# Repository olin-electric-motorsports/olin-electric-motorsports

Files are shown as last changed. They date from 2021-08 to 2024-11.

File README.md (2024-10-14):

<h1 align="center">
	Olin Electric Motorsports
</h1>

Welcome to the Olin Electric Motorsports monorepo. This is the home for all of our
electrical, firmware, and software work.

This document will help you get started contributing and walk you through
important steps for collaborating with teammates.

## Getting Started

### For new members:
Make sure you have a GitHub account. If you don't, create one on [GitHub](github.com) (this website). Make sure to save your username, email, and password. This will be useful in the next step. Once you have an account, STOP, and ask a lead/senior engineer to add you to the `olin-electric-motorsports` org.

Once you've successfully installed Ubuntu, have a GitHub account, and have ben added as an org member: on your computer, open a terminal (press the Windows key and type `term`, then hit `Enter`).

Install `git` on your computer if it's not already.
```shell
sudo apt install git -y
```

Also install python3
```shell
sudo apt update && sudo apt install python3
```

One last Python library...
```shell
sudo apt-get install python3-distutils
```

### Linking a Computer to your Account
We need to connect your GitHub account to your computer's specific git instance \(created by the command you just ran\). We do this for safety: someone pretending to be you can't add code to our repo!
1. Set your username:
```shell
git config --global user.name 'your username here'
```

2. Set your email address:
```shell
git config --global user.email 'your email here'
```

3. Create the SSH Key \(essentially a super crazy passord\). When you’re prompted to "Enter a file in which to save the key," press `Enter`. This accepts the default file location. At the password prompt, hit `Enter` again.
```shell
ssh-keygen -t ed25519 -C "your_email@example.com"
```

4. To see your SSH Key, run the following command. Copy the whole contents of the output to your clipboard (you won't be able to copy or paste in the terminal using ctrl+c and ctrl+v, instead use ctrl+shift+c and ctrl+shift+v or right-click to do it graphically).
```shell
cat ~/.ssh/id_ed25519.pub
```

5. In your github page, go to your profile \(Top Right\) > `settings` > `SSH and GPG Keys`. Click on the green `New SSH Key` button. Title your key as `Olin Computer` and paste in your SSH key. Finally, click the green `Add SSH Key` button. Nearly done!
6. Test your ssh connection by using the command below. Type `yes` when prompted. You've done this step correctly if you see something along the lines of `Hi "username"! You've successfully authenticated, but GitHub does not provide shell access.`
```shell
ssh -T git@github.com
```
### Creating your OEM environment
Clone this repository into a folder of your choice (many people
choose to put it in `~/Documents`.

```shell
cd ~/Documents
git clone git@github.com:olin-electric-motorsports/olin-electric-motorsports.git
```

Once you have it, cd into the repo and install the KiCad Git filters (a set of rules that remove temp files that can cause clutter):

```shell
cd olin-electric-motorsports/
./scripts/install_kicad_git_filters.sh
```

You'll also want to have the KiCad Git Hooks to generate our symbol libraries. These hooks run every time you push or pull and allow multiple users to add symbols/footprints to our KiCAD library.

```shell
./scripts/install_kicad_git_hooks.sh
```

### Installing AVR and tools
Next, install the AVR toolchain:

```shell
sudo apt install gcc-avr avrdude avr-libc binutils-avr gdb-avr
```

### Installing Cantools
You need to be able to hear to our MCUs on the car!
```shell
pip3 install cantools
sudo apt install can-utils
```

### Installing Bazel

Next, install Bazelisk. Run this massive blob and you should be good to go.

```shell
sudo apt install apt-transport-https curl gnupg -y
curl -fsSL https://bazel.build/bazel-release.pub.gpg | gpg --dearmor >bazel-archive-keyring.gpg
sudo mv bazel-archive-keyring.gpg /usr/share/keyrings
echo "deb [arch=amd64 signed-by=/usr/share/keyrings/bazel-archive-keyring.gpg] https://storage.googleapis.com/bazel-apt stable jdk1.8" | sudo tee /etc/apt/sources.list.d/bazel.list
sudo apt install bazel-5.4.0
```

You should now be able to run the following without error (after changing your directory to be in
the `olin-electric-motorsports` folder):

```shell
bazel build --config=16m1 //examples/16M1/blinky -c opt
```

> [!NOTE]
> If you get an error message stating 'env: python: No such file or directory', ensure that the PATH environment variable is properly established. This can be done by adding the file to your .bashrc file:
> ```
> export PATH=$PATH:/usr/local/bin
> ```

### KiCad Setup

To install KiCad on Ubuntu, run the following: Type `Y` when prompted.

```shell
sudo add-apt-repository --yes ppa:kicad/kicad-8.0-releases
sudo apt update
sudo apt install --install-recommends kicad
```

Open KiCad (windows key and type KiCAD) Click on the Blue App (always do this when opening Kicad - otherwise you can corrupt files!). Hit `Enter` if asked about settings imports and auto-updates for add-ons.
From the top bar, open _Preferences > Configure Paths..._. Add a new row to the table using the plus button (you will have to fill out TWO fields... shown below):

Name | Path
-----|-----
OEM\_DIR|`/home/your-username/Documents/olin-electric-motorsports`

Click `OK`, then again from the top bar, open _Preferences > Manage Symbol Libraries ..._.
Same deal as before with the new line at the bottom, new values though this time:

Name | Path
-----|-----
OEM |`${OEM_DIR}/parts/schematic/oem.kicad_sym`

> [!WARNING]
> If you get an error, you either typed something incorrectly or haven't generated the OEM symbol library ever before.
> To generate:
> 1. navigate to the base `olin-electric-motorsports` directory in a terminal.
> 2. run python3 tools/symbols/convert.py symbols2library
> 3. path to symbol files: parts/schematic/oem
> 4. path to library file: parts/schematic/oem.kicad_sym

Click `OK`, then again from the top bar, open _Preferences > Manage Footprint Libraries ..._.
3rd time's the magic one, plus button, add the values in the table below.

Name | Path
-----|-----
OEM |`${OEM_DIR}/parts/oem.pretty`

where `your-username` is the username on your computer.
If you cloned our repository into a different directory than the `~/Documents` folder, this is just an absolute path to the repo.

Visit [this page](https://www.kicad.org/download/) to find instructions for
downloading KiCad for other operating systems.

## Integration Resources
### Flashing to microcontrollers

> [!CAUTION]
> Take care to plug in the programmer correctly. If you insert it the wrong way, you have the potential to reverse-bias sensitive electronics (you could smoke them)!

To flash (program) an ATMEGA16m1 microcontroller, use a variation of the following command:
```shell
need to insert example flashing command here
```

To flash (program) an ATMEGA16m1 microcontroller using the btldr (remote CAN flashing), use a variation of the following command:
```shell
need to insert example can flashing command here
```

### Viewing CAN data/the canviewer
First, plug a CAN-to-USB dongle into your computer and connect CAN+ and CAN- to the car or test platform's CAN port.

To initalize the dongle, run the following command:
```shell
need to insert example can init command here
```

### Cantools
1. `candump`: A tool for streaming CAN frames as they are sent. Useful for short captures or slow data.
2. `cansniffer`: Similar to candump, but messages with the same ID replace each other for easier viewing (a table).
3. `cansend`: Use this tool to send CAN frames from your computer. CAN (oh the puns will never end) be helpful when debugging boards or to program modules like the motor controller or G-Meter.

### CANViewer
OEM has designed a custom Python CAN GUI to monitor the car's state.
Type the following command to run the viewer.
```shell
need to insert CANViewer command here.
```

### Contributing

If you are working on a new project, the first step is to make sure you have the
latest code:

```shell
git pull origin main
```

### Onboarding stop here...

Next, create your feature branch (only do this once you have a project!):

```shell
git switch -c your-username/feature-name origin/main
```

Now, you can start working on code, committing on your branch, and eventually
opening up a pull request to `main`.

New projects should be placed into a folder within the `//projects` directory
(for instance, `//projects/hitl/`. Hardware and firmware that run on MKV or MKVI
should go in the proper subfolder within `//vehicle`.

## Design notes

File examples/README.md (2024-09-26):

# Examples

The `examples/` directory will house code samples and hardware samples for
people to reference. Examples will include

* Blinky for the ATMega16m1
* Blinky for the STM32F103C8T6 (not finished)
* Simple ATMEGA KiCad schematic/layout (not finished)

as well as others.

## To-Do

* Who will own this folder? Who will keep it up to date, add new content, make
  sure things are correct, etc?

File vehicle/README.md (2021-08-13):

# Vehicle

The boards and code for the different vehicles that the team builds will exist
in this folder.

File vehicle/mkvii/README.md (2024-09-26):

# MKVI

The development of boards for the Mark VII car will go in this folder.
Here's to a great year everyone!

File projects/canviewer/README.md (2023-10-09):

# OEM CAN Dashboard

Welcome! Here lies the documentation for the use of the CAN dashboard GUI on our team.

The dashboard uses a QT GUI and includes support for SocketCan (for example, the PCAN dongles) as well as our new Seeedstudio dongles.

It also is fully configurable via YAML.

## Using the tool
1. Set up your CAN device if you are using a PCAN or other socketcan device. Instruction for this can be found [here](https://coda.io/d/_dbuFnC2EA_e/How-to-use-CAN_suzvC)
    - You can also use this tool with a virtual CAN bus
2. Run the tool! This is done using the command `bazel run //projects/canviewer`. There are three command line arguments as well
    - `-b` - Either `seeedstudio` or `socketcan` 
    - `-c` - Channel
        - Socketcan: this is the network interface name you created when setting up your device (usually can0 for real hardware or vcan0 for a virtual CAN bus)
        - Seeedstudio: this is the _device path_ for your CAN dongle. Typically this will be something like `/dev/ttyUSB0`. The best way to find it is to run `ls /dev/ttyUSB*`, which lists all the USB device paths, before and after you plug in your dongle to find the one that was added. The number starts at 0 and increments every time something is plugged in, so if you unplug and replug your CAN dongle, the number will change!
    - `-d` - the DBC file to be used to decode the CAN messages. This is specified as a file path starting from the root of the monorepo.
        - This has a default value of `vehicle/mkvi/mkvi.dbc` - in other words, if you want to decode messages from MKVI or a MKVI board, you do not need to specify this argument. If you're reading this in future years, feel free to update the default value in a new PR - just be sure to add your DBC as a dependency in the BUILD file for this project.
        - You can check `//vehicle/mkvi/BUILD` to see which DBC/YAML files are included in the master DBC
    - These arguments would be passed like so for a bustype of seeedstudio and a USB device at /dev/tty/USB0 when plugged into MKVI:
        ```
        bazel run //projects/canviewer -- -b seeedstudio -c /dev/tty/USB0
        ```
        The two dashes signal the end of the arguments to bazel and any remaining ones will be passed to the CAN viewer.
    
## Configuring the tool

To change the signals that are displayed in the first two columns, simply add or remove the signal names from underneath their respective column headers in the YAML. For example, if I wanted to see the IMD status in the Vehicle Values section, I would add this line under the vehicle values header
```
imd_status:
```
Note the colon at the end - it is required.

The states section is formatted like so:
```
air_control_critical: # Message name
  air_state: # State signal
  air_fault: # Fault Signal
```
Again, note the indentation and the colon - they are part of the YAML format.

If you would like to apply a processing function to process the value one of the signals in the vehicle values column before displaying it:
1. Define the function in the `projects/canviewer/utils.py` file
2. Specify it in the YAML by setting the signal's value to a dictionary with `processing_function` as a key and the function name as its value, like so:
```
# Vehicle Values
max_temperature:
  processing_function: convertVtoT
min_temperature:
  processing_function: convertVtoT
pack_voltage:
air_p_status:
...
```

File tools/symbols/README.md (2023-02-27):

# Symbol Converter

## Usage

### `symbols2library`
Convert symbols to `.kicad_sym` library.

If you have installed the git hooks (`./scripts/install_kicad_git_hooks`), this will run automatically after each `git checkout`.

Example:

```bash
bazel run //tools/symbols:convert -- symbols2library --source /mnt/data/Formula/olin-electric-motorsports/parts/schematic/oem -o /mnt/data/Formula/olin-electric-motorsports/parts/schematic/oem.kicad_sym
```

### `library2symbols`
Convert a `.kicad_sym` library to symbols.

If you have installed the git hooks (`./scripts/install_kicad_git_hooks`), this will run automatically during each `git commit` and add symbol files to the commit.

If you do not wish to have this happen you can `git commit --no-verify` instead and then manually run the script.

Example:

```bash
bazel run //tools/symbols:convert -- library2symbols --source /mnt/data/Formula/olin-electric-motorsports/parts/schematic/oem.kicad_sym -o /mnt/data/Formula/olin-electric-motorsports/parts/schematic/oem
```

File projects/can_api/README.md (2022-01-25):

# Generated CAN API

The purpose of this project is to create a tool that automatically generates C
code that abstracts CANbus interaction for microcontrollers.

## Context

Before 2021, our team used a CAN API that allowed for sending byte-arrays with a
specified ID. In 2021, we developed a new library that used semantics of the C
language like structs and enums to develop a cleaner library that allowed for
initializing, sending, and receiving messages, with options for polling and
interrupts.

However, none of these specified the IDs or the contents of the messages. For
that, we used the MKx CAN Address Space, a Google Sheet that listed all of the
messages and all the different signals. This was the "single source of truth"
that all the application code referenced.

The new generated CAN API is a layer of abstraction that utilizes the CAN
library as a network layer. Messages and their signals are defined in YAML
files.

## Scope

The project is designed to be _robust_ and as _reusable_ as possible. Most of
the project is unit-tested. The backend of the project uses an external library
called [cantools](https://github.com/cantools/cantools), which is thoroughly
tested.

### Goals

* A DBC file can be generated from the individual YAML files
* All message collisions are detected at compile-time
* A `.c` and `.h` file are generated for each YAML file that include send and
  receive functions for each of the messages sent and received by the ECU as
  specified by the YAML file

### Non-goals

* _Getters_ and _setters_: Functions of these types are used to set the values
  of signals in a CAN message (like `set_bspd_brakelight_voltage(uint16_t
  voltage)`). These could be useful, but for now, we opt to use global variables
  because they have a simpler implementation.
* Message ID assignment: This could be a future goal, see __Future Work__ below

## Usage

To begin, we must define a YAML file for the ECU. As an example, we will use the
BMS ECU. The file we are writing will be in `vehicle/mkv/software/bms/bms.yml`.
We begin with the name of the node/ECU, _bms_:

```yaml
# vehicle/mkv/software/bms/bms.yml
name: bms  # Name of the ECU
```

Next we specify the messages received by the ECU. For example, the BMS should
receive the AIR Control Critical message, so we can specify the following:

```yaml
# All the received messages
subscribe:
  - name: air_control_critical
    mob: 1
```

This says that the BMS should listen for the `air_control_critical` message
(this name is specified as the `name` of a message in a different YAML file),
and that it should use message object (MOb) 1.

__Note that this code _only_ allows for receiving a specific CAN message per
MOb, not multiple. If you need to listen to a range of messages, don't use the
API.__

Now we specify the messages _sent_ by the ECU. Let's take the following row from
the MKV CAN Address Space as an example:

Name | ID | Length | Frequency (Hz) | Byte0 | Byte1 | Byte2 | Byte3 | Byte4 | Byte5 | Byte6 | Byte7
-----|----|--------|----------------|-------|-------|-------|-------|-------|-------|-------|------
BMS Core|0x10|8|16|Fault Code|Relay Status|Temperature|Pack Voltage|SOC Estimate|BMS OK|Current-limiting enabled|Cell-balancing status

The MKV CAN Address space specified that the minimum size of any signal is 1
byte. However, with our system, we can have signals that are smaller (like a
single bit). Here's how we might represent the message in a new way:

```yaml
publish: - name: bms_core
    id: 0x10
    freq_hz: 16
    signals:
      - name: fault_code
        slice: 0 + 8  # This is (start bit) + (length)
        unit:
          type: enum
          values:
            - NO_FAULT
            - FAULT_EXAMPLE_1
            - FAULT_EXAMPLE_2
            - ...
      - name: temperature
        slice: 8 + 8
        unit:
          type: uint8_t  # C-type that this is stored as
          name: degC  # Used for displaying when decoding information
          offset: 0  # Offset used to calculate the true value
          scale: 5 / 4096  # Scale used to calculate the true value
      - name: pack_voltage
        slice: 16 + 8
        unit:
          type: uint8_t
          name: V
          offset: 0
          scale: 1000
      - name: soc  # State of Charge
        slice: 24 + 8
        unit:
          type: uint8_t
          name: "%"
          offset: 0
          scale: 100 / 4096
      - name: relay_state
        slice: 32 + 1
        unit:
          type: bool  # Bool is used for any value where it is either 0 or 1
          values:
            t: Relay open  # String to display when value is true
            f: Relay closed  # When value is false
      - name: bms_ok
        slice: 33 + 1
        unit:
          type: bool  # Bool is used for any value where it is either 0 or 1
          values:
            t: BMS OK
            f: BMS NOT OK
      - name: current_limiting_enabled
        slice: 34 + 1
        unit:
          type: bool  # Bool is used for any value where it is either 0 or 1
          values:
            t: Current limiting enabled
            f: Current limiting disabled
      - name: cell_balancing_status
        slice: 35 + 1
        unit:
          type: bool  # Bool is used for any value where it is either 0 or 1
          values:
            t: Cell balancing active
            f: Cell balancing inactive
```

Notice that we have reordered some of the fields. This is because it is better
to group signals together if they are less than a byte so that they can be
"packed" together. If we had a 1-bit signal followed by an 8-bit signal followed
by a 1-bit, it would require at least 3 bytes of space since full bytes must be
aligned.

Now that we have our completed file, we can define our CAN API using Bazel. In
the `BUILD` file, we will load a rule and create a new target:

```python
# vehicle/mkv/software/bms/BUILD

load("//bazel/tools:defs.bzl", "can_api_files")

...

# Must include this
exports_files([
    "bspd.yml",
])

# Defines the CAN API library
can_api_files(
    name = "can_api",
    dbc = "//vehicle/mkv:mkv.dbc",
    yaml = ":bspd.yml",
)
```

In addition, we should add the BMS YAML file to the list of MKV YAML files in
`vehicle/mkv/BUILD`:

```python
# vehicle/mkv/BUILD
load("//bazel/tools:defs.bzl", "dbc_gen")

# Generates DBC
dbc_gen(
    name = "mkv.dbc",
    srcs = [
        "//vehicle/mkv/software/air_control:air.yml",
        "//vehicle/mkv/software/brakelight_bspd:bspd.yml",
        "//vehicle/mkv/software/motor_controller:motor_controller.dbc",

        # New
        "//vehicle/mkv/software/bms:bms.yml",
    ],
)
```

We do this so that we can use the DBC generator to link all of these YAML files
together into a single DBC.

Now that we have our CAN API created, we can test to make sure that it works:

```shell
$ bazel build //vehicle/mkv/software/bms:can_api
```

If this builds successfully, then the CAN API generation is working.

We can add `:can_api` to the `deps` field of our `cc_firmware` that defines the
BMS code. Then, in our BMS file, we can start using the API. The following
features are documented:

#### Setting signal values

In order to set the value of a signal, we use a struct. The CAN API generates a
struct whose fields are each of the signals of the message. For example, the
struct for the `bms_core` message defined above might look like:

```c
struct can_tools_bms_core_t {
    uint8_t fault_code;
    uint8_t temperature;
    uint8_t pack_voltage
    uint8_t soc;
    uint8_t relay_state;
    uint8_t bms_ok;
    uint8_t current_limiting_enabled;
    uint8_t cell_balancing_status;
};
```

__Note that even though the length of, for example, `relay_state` should be 1
according to the YAML, the struct will store it as a byte. This is because
before the message is sent using the `can_send` function, there is another,
private function that "packs" the message according to the correct lengths. So
the value of the `uint8_t relay_state` will be packed into a single bit when the
message is sent__.

The CAN API also defines a single variable of this type as `struct
can_tools_bms_core_t bms_core`. That way, you can access it like so:

```c
// Set the pack_voltage
bms_core.pack_voltage = get_pack_voltage();

// Set the relay_state
bms_core.relay_state = gpio_get_pin(BMS_RELAY);
```

This is the same variable that is used when sending the CAN message, so care
should be taken that there are no concurrency issues (say, if a value is set
during an interrupt which occurs while a CAN message is being sent).

#### `can_init_{ecu}`

This replaces/wraps the `can_init` function. Currently, there is no additional
functionality, but in the future it could be used to initialize certain
ECU-specific things, or could be useful if more than one CAN bus existed on the
car.

#### `can_send_{message}`

This sends a specific CAN message. For example, to send the _BMS Core_ CAN
message, we could call `can_send_bms_core();`. This will take the aforementioned
`bms_core` variable (with all of the signals as struct fields), pack it into a
byte array, and send it as a CAN message.

#### `can_receive_{message}`

This receives a specific CAN message. In order to receive the _BMS Core_
message, we call `can_receive_bms_core();`. This function will return
immediately. The following table gives the return codes:

Return Code | Meaning
------------|--------
`0`|Data is ready
`1`|Fatal error occured
`-1`|Message not received

If a `0` is returned, we can access the data in the message struct (i.e.
`bms_core`).

### DBC Generation

The final feature of the project is DBC generation. As we saw, when we declare a
YAML file, we can also add it to the `srcs` of a `dbc_gen` target, like the one
in `vehicle/mkv/BUILD`. In general, we want to have one DBC per vehicle. In
order to build the MKV DBC, we can run:

```shell
$ bazel build //vehicle/mkv:mkv.dbc
```

Then we can access the DBC file in `bazel-bin/vehicle/mkv/mkv.dbc` and use it in
Wireshark, BusMaster, or any other software that uses a DBC.

## Concurrency

__⚠️ Important Usage Note. ⚠️__

The `can_send_{{ message }}` function must _not_ be called from an interrupt
context. If it is, there can be unpredictable behavior. In general, special care
should be taken around interrupts and concurrency. There is a global, `volatile`
variable for the CAN data containing each of the signals, and this struct is
used in the `can_send` function. Thus, if the `can_send` function happens in an
interrupt that occured when a variable was in the middle of being updated, the
data can become garbled.

The `can_send` function is wrapped in atomic block, meaning that during its
execution, no interrupts will occur.

## Future Work

In the future, it would be great if the IDs were automatically generated based
on message priority and deadline. There is a
[paper](https://www-users.cs.york.ac.uk/~robdavis/papers/RTNS2016_can_extend.pdf)
that describes an algorithm that can be used to optimally generate CAN IDs, and
this could be interesting to implement later on. But since our CANbus is so
under-utilized, there isn't really any urgency.

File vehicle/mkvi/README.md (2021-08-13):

# MKVI

The development of boards for the Mark VI car will go in this folder.

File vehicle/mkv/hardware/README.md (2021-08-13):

# Vehicle Hardware

The subfolders in this folder will be for the different PCBs that will go on the
car for the current season. This may be things like the BMS, the dashboard, and
the AIR control boards.

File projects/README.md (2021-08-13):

# Projects

The `projects/` directory will house projects that are under active and volatile
development. This will include things like advanced research projects that won't
make it onto the vehicle during the current season, _as well as_ projects that
are parallel to the car, like the HIL system.

Once a car-related project has matured enough, it will be moved into the
`vehicle/` directory, where development may continue to integrate it into the
vehicle of the season.

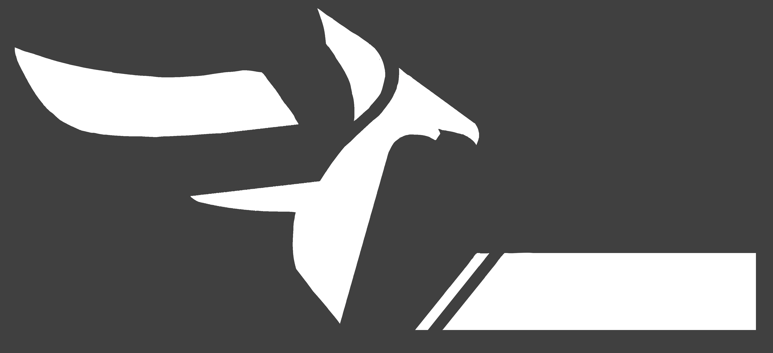
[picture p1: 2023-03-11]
vehicle/mkvi/hardware/service-section/motherboard/Art/WHITE_motherboard_a_top_pcb.png

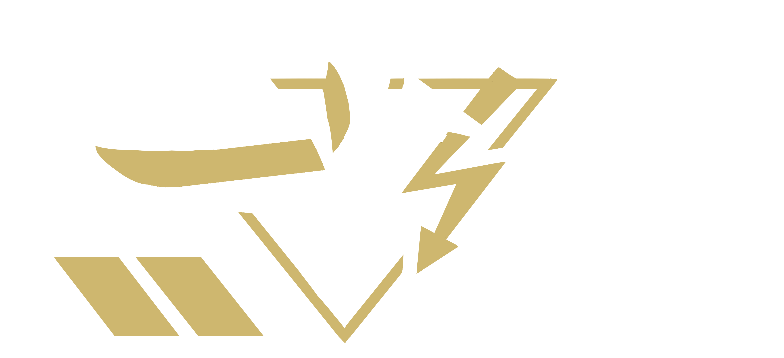
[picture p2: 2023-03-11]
vehicle/mkvi/hardware/service-section/motherboard/Art/GOLD_motherboard_a_top_pcb.png

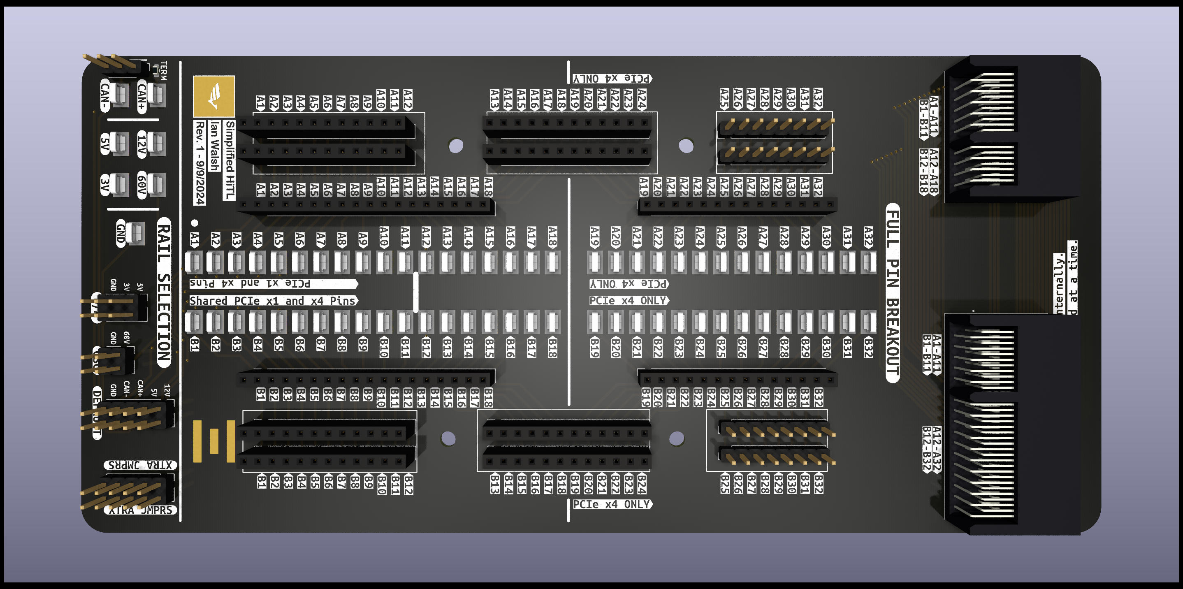
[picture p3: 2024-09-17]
projects/PCIe Development/pcie_breakout/breakout_pcie.png

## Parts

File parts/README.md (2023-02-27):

# KiCad Parts
KiCad library employed by Olin Electric Motorsports electrical team.

## Libraries

We are starting a fresh KiCad libraries for Mk. 6. The goal is to ensure that we do not incorporate components that are not stocked and to increase the quality and consistency of our libraries. The new library allows us to better track the status of components and support multiple purchasing options.

| Path | Description |
| ---- | --- |
| `/parts/3DModels/` | 3D Models for Mk. 5 era |
| `/parts/footprints.pretty/` | Footprints library for Mk. 5 era |
| `/parts/schematic/formula.kicad_sym` | Schematic symbol library for Mk. 5 era |
| `/parts/mk6.3dshapes/` | 3D Models for Mk. 6 |
| `/parts/mk6.pretty/` | Footprints library for Mk. 6 |
| `/parts/schematic/mk6.kicad_sym` | Schematic symbol library for Mk. 6|

## Guidelines

> Note: Some older parts do not follow this guidelines completely. For this reason, double check when copying over any legacy components.

1. General symbol naming guidelines

> Prior to Mk. VI we used a global library, however it was poorly maintained and many of the components are no longer available for purchase. New projects must use the OEM libraries.

Open KiCad. From the top bar, open up _Preferences > Manage Symbol Libraries..._. Add new rows to the table:

Nickname | Library Path
---|---
formula |`${OEM_DIR}/parts/schematic/formula.kicad_sym`
OEM | `${OEM_DIR}/parts/schematic/oem.kicad_sym`

From the top bar, open up _Preferences > Manage Footprint Libraries..._. Add new rows to the table:

Nickname | Library Path
---|---
footprints |`${OEM_DIR}/parts/footprints.pretty`
OEM | `${OEM_DIR}/parts/oem.pretty`

# Guidelines

## Symbols

Applies to all symbols in the `OEM` library. When a new schematic symbol is added it must be checked against these guidlines.

### Naming

For specific parts such as ICs, use the general part number (e.g. `ADBMS1818` not `ADBMS1818-WASZ-RL`). For passives and other generic components, a descriptive (e.g. `R_200`) name is suitable.

### Required Fields

Field | Example | Show |  Description
--- | --- | --- | ---
Reference | `R` | Y | [Letter corresponding to component type](https://klc.kicad.org/symbol/s6/s6.1/)
Value | `10K` | Y |  Value of component or part name
Footprint | `OEM:R_0805` | N | Reference to footprint for component
Datasheet | `https://www.example.com/.../datasheet.pdf` | N | Link to datasheet
MPN | `RCA080510K0FKEA` | N | Manufacturer Part Number for ordering
MFN | `Vishay` | N | Manufacturer (not to be confused with distributors like digikey)
DKPN | `541-2226-2-ND` | N | Digi-Key Part Number for ordering (name of disitributor if not available through DK)
Package | `0805` | N | Component package (if a common package)
NewDesigns | `Yes` | N | If the component should be used in new designs. If a component should not be used set to `DO NOT USE` and enable `Show`.
Stocked | `Tape` | N | Should we keep this part on hand, if so what format
Style | `SMD` | N | `SMD` or `THT` or `Custom`. Useful for filtering BOMs for assembly service

### Required Metadata

Property | Notes
--- | ---
Symbol Name | Do not include formula, OEM, MkVI, etc.
Description | Part description for search
Keywords | Comma separated list of search terms

### Component Specific Fields

In addition to the required fields, some component types have additional required fields to help with design reviews. If there is any specification you think is important to the component, add it as a field in addition to the required fields.

#### ICs

Field | Example | Show |  Description
--- | --- | --- | --- | 
SupplyVoltage | `2.5-5.5V` | N | The supply voltage for the IC
LogicLevel | `5V` | N | If applicable, the logic level for IO

#### Connectors

Field | Example | Show |  Description
--- | --- | --- | --- | 
RatedVoltage | `600VDC` | N | Rated voltage - must be documented in datasheet or link source
ContactCurrent | `.8A` | N | Rated current per contact
MatesWith | `MPNABCD` | N | Symbol name of mating connector. If there are multiple mating connectors `MatesWithAltX` fields may be added.

#### Passives

The relevant specifications vary for different passives. Make sure any specifications that were relevnt to your selection are included as fields and listed in the description. This makes finding suitable alternatives easier if there are supply issues.

### Symbol Design

1. If multiple pins should **always** be connected together, use [pin stacking](https://klc.kicad.org/symbol/s4/s4.3/).
    - Do not stack power pins if they require seprate decoupling capacitors
1. Pin orientation
    * Power pins must be placed on the top of the symbol
    * GND pins must be placed on the bottom of the symbol
    * Input pins must be placed on the left of the symbol
    * Output pins must be placed on thr right of the symbol
    * For some components, pins can function as inputs or outputs. In this case they should be placed on the right of the component.
1. Pins should be grouped functionally, not based on pin order

## Footprints

Applies to all footprints in the `OEM` library. When a new footprint is added it must be checked against these guidlines.

Do not create footprints for specific components, create footprints for packages so that they can be reused. Add alternate package names to the description.

In the rare case that a component does not have a package name, the symbol name must be matched exactly.

When possible, use KiCad's built-in footprints and save a copy to the OEM library. This ensures our library is stable and updates to built in packages do not unexpectedly break anything.

### Naming

We loosely follow the [KiCad Library Conventions for footprint names](https://klc.kicad.org/footprint/f3/). Generally, we err on the side of slightly simpler, easier to remember footprint names.

For example, we omit the metric sizing in SMT passives (i.e. `R_0805` instead of `R_0805_2012Metric`).

For connectors, we follow `[Series]_[PinLayout]_[Orientation]`. For example, `MicroFit_2x4_RA`.

Orientation | Shorthand
--- | ---
Vertical | VT
Horizontal | RA
45 degree | 45

### Required Fields

Field | Example | Show |  Description
--- | --- | --- | --- | 
Source `https://example.com/.../mpn.pdf` | N | Datasheet with footprint drawing.

### Required Metadata

Property | Notes
--- | ---
Symbol Name | Do not include formula, OEM, MkVI, etc.
Description | Part description for search. Include alternate package names
Keywords | Comma separated list of search terms

### Footprint Design
Getting footprints online is encouraged, but sometimes they aren't perfect.

1. On ICs, Pin 1 must be marked with two dots and an extended line over the pin. The dots must have a radius of 0.3mm.

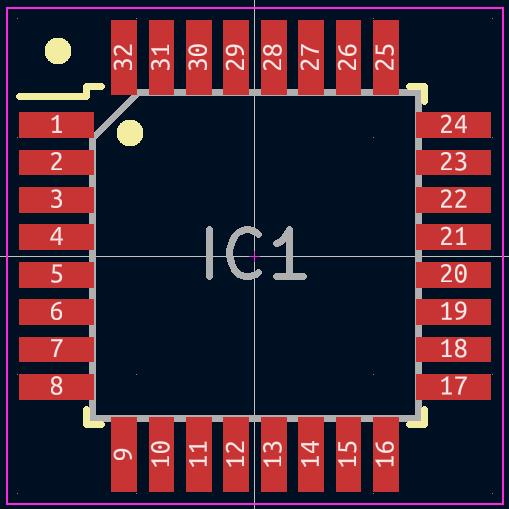
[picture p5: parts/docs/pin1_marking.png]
    
1. For polar components, the component outline must not extend around the anode. Additional markings should not be used.

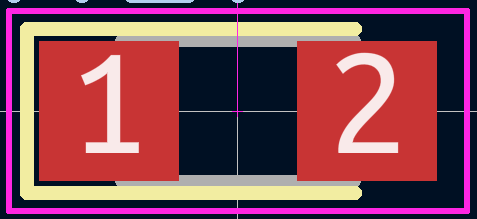
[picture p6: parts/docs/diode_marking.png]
screenshot of diode with marking
    
1. Through hole components must indicate pin 1 with a square pad.

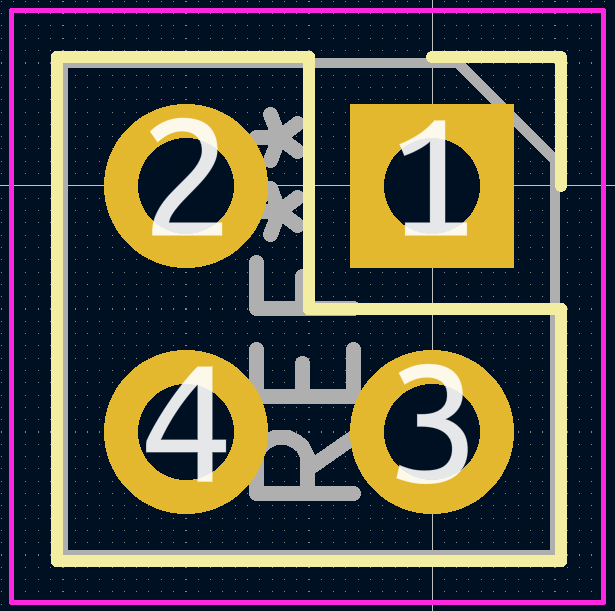
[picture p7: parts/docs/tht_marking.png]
    
1. Silksreen designs in component footprints must be drawn with a line width of 0.12mm.

1. The reference designator should be set to the `User.Comments` layer or hidden to avoid cluttering the silkscreen.

## 3DModels

All footprints must include a 3D Model.

All 3D Models must be placed in the `OEM.3dshapes`. Do not create subdirectories for individual 3D models. Add only the 3D model files required for each component. The name of each file must match the associated footprint. If multiple footprints use the same 3D model, the name should match the most generic footprint.

If possible, models should not require positioning or scaling to match the footprint.

* 3D Model Naming Guidlines

    The name of 3D Models should match the footprint name.

Guidelines are based off [KiCad Library Convention](https://klc.kicad.org/).

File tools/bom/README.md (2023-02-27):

# Unified BOM tool

## Usage

### `join`
Joins a number of BOMs into a single BOM grouped by DigiKey Part Number for ordering.

Requires a input CSV with columns `Name`, `Count`, `BOM`. Column names are case insensitive, order doesn't matter and additional columns will be ignored. The bom for each board is multipled by the desired count before joining into the final BOM. Each BOM must include `Count` and `DKPN` columns. This is useful for large batch order with multiple boards that share components. The resulting file can be edited to meet minimum quantities or add additional parts.

Example:

```bash
bazel run //tools/bom:join -- --map /mnt/data/Formula/olin-electric-motorsports/vehicle/mkvi/boards.csv -o /mnt/data/Formula/olin-electric-motorsports/vehicle/mkvi/bom.csv
```

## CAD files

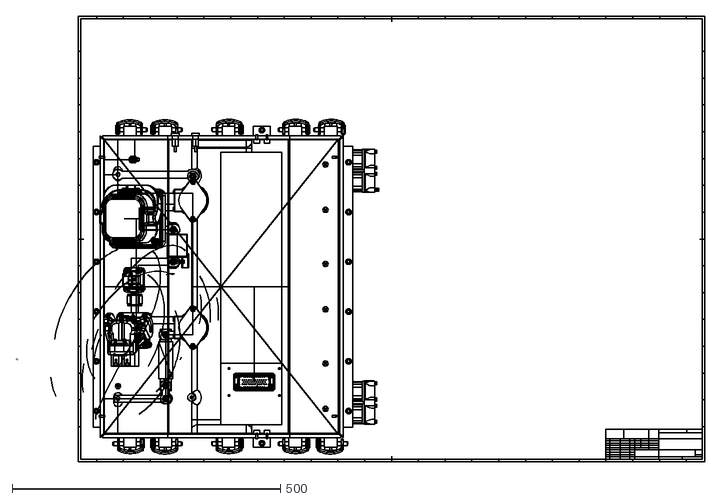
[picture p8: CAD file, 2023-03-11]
vehicle/mkvi/hardware/service-section/motherboard/6-AC0-ASSEMBLY-MOTHERBOARD-REFERENCE.DXF
1284.8 x 831.0

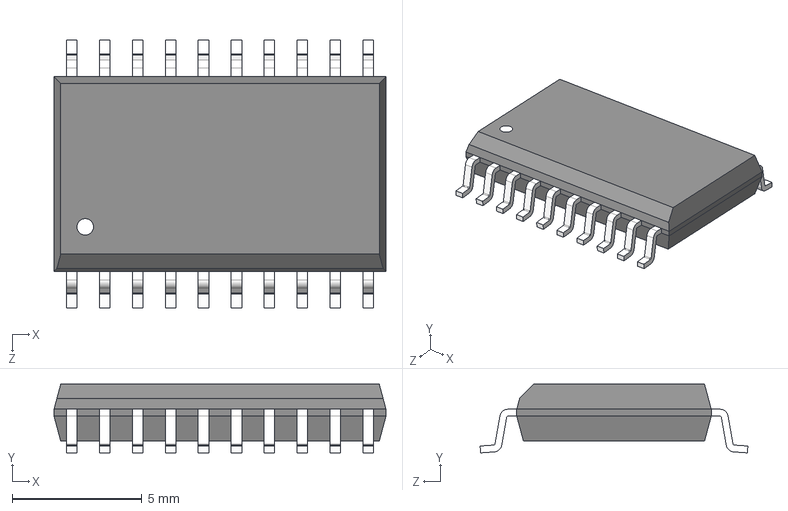
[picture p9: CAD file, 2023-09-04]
parts/3DModels/20-SOIC/20-SOIC.STEP
12.8 x 2.65 x 10.3 mm

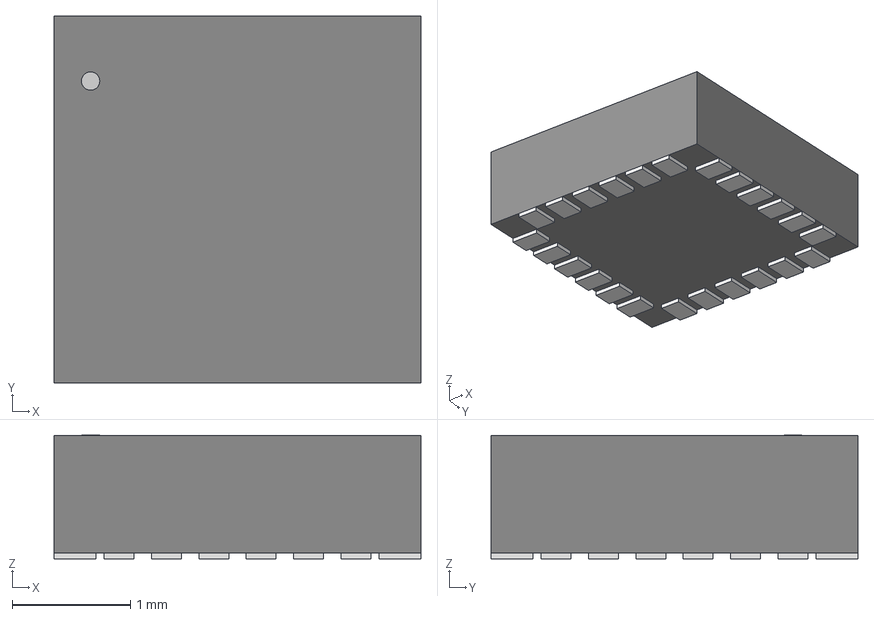
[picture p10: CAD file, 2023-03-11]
parts/3DModels/24-QFN/24-QFN.step
3.10 x 3.10 x 1.04 mm

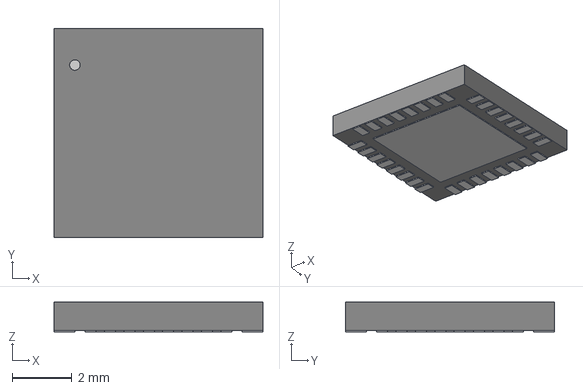
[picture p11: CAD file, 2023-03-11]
parts/3DModels/32-QFN/PV_ATM.step
7.00 x 7.00 x 1.00 mm

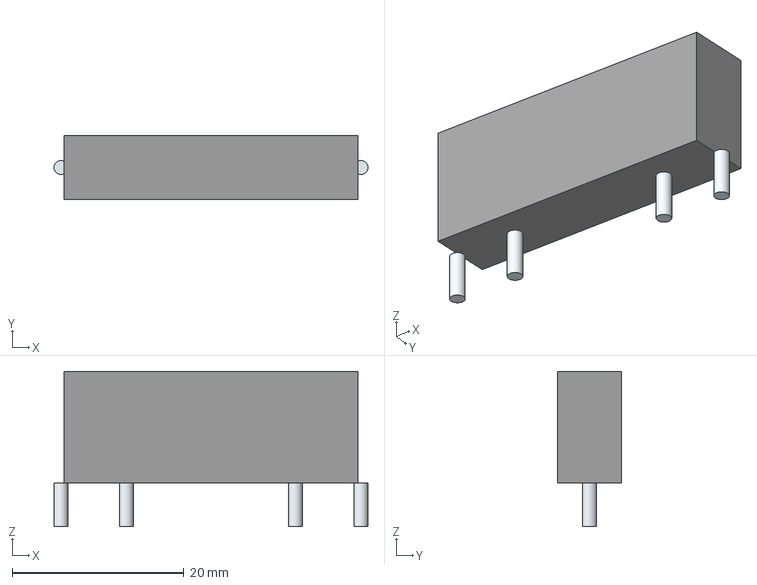
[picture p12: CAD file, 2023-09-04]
parts/3DModels/3AG_fuse_holder/3AG_fuse_holder.stp
36.6 x 7.49 x 18.1 mm
Leads x 4

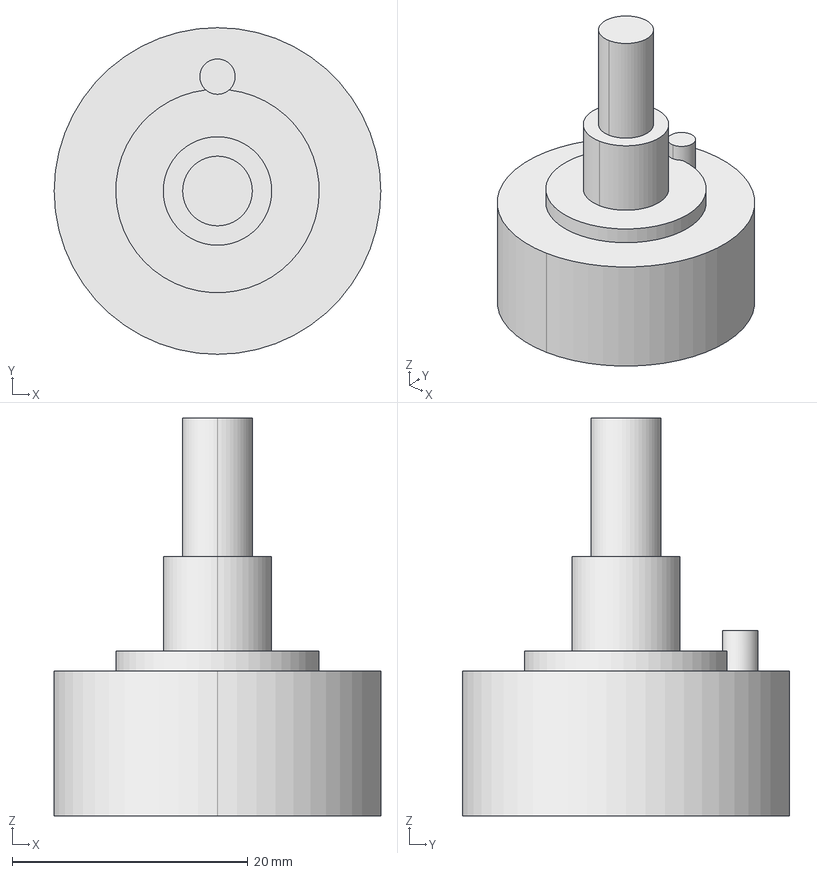
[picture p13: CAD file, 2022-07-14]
parts/3DModels/3P4T_rotary_switch/prog_switch.step
27.7 x 27.7 x 33.8 mm

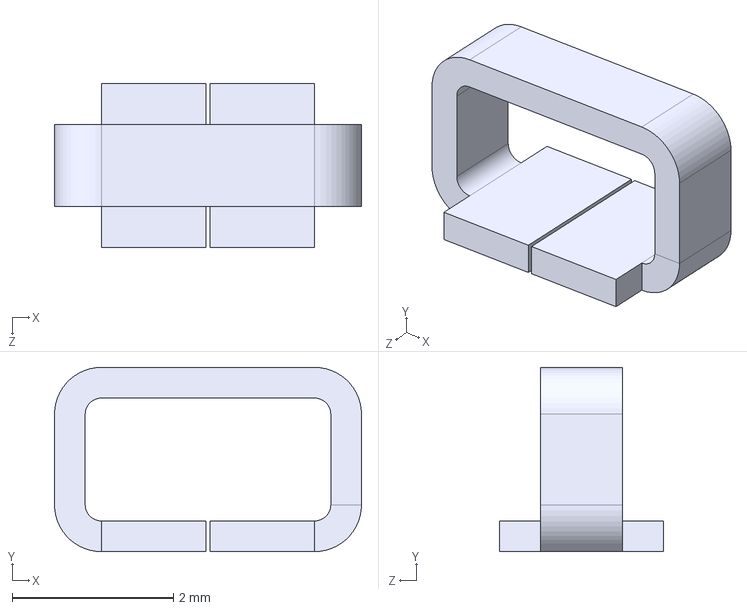
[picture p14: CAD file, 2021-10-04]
parts/3DModels/5029-smdTestPoint/5019--3DModel-STEP-56544.STEP
3.81 x 2.29 x 2.03 mm

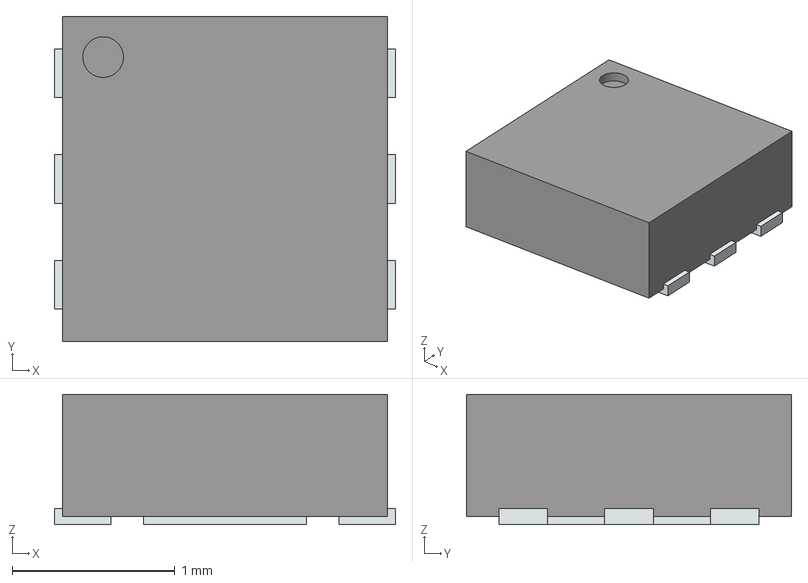
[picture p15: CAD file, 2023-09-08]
parts/3DModels/6-WDFN/6-WDFN.stp
2.10 x 2.00 x 0.8 mm
ThermalPin
PinsArrayLR

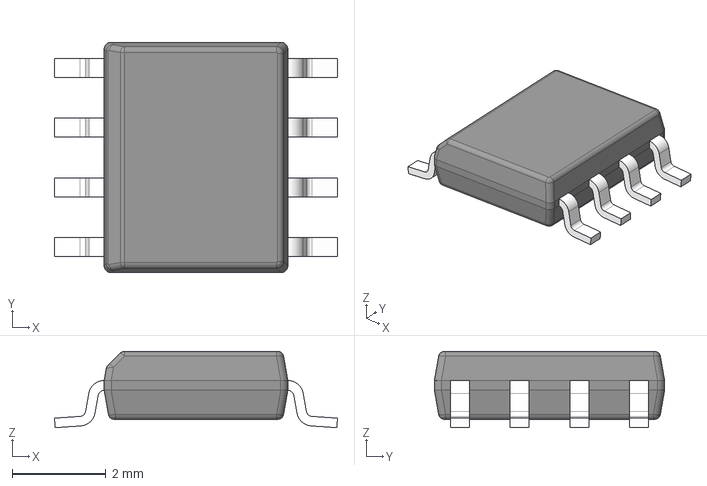
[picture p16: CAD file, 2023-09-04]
parts/3DModels/8-SOIC/8-SOIC.stp
6.02 x 4.90 x 1.63 mm
BODY-SO
LEAD-D0008A x 8

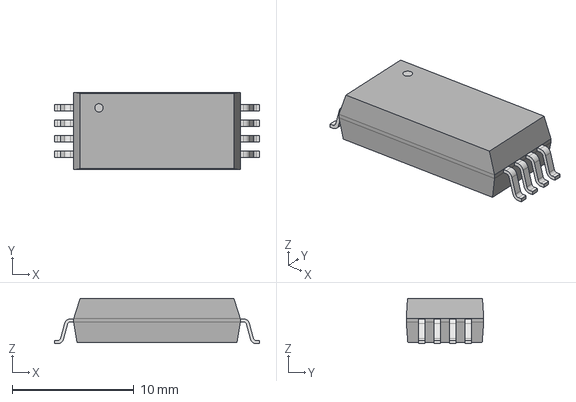
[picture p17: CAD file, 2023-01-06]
parts/3DModels/ACN-H50L-Stretched-SO8_BRA_Optoisolator/ACN-H50L-Stretched-SO8_BRA.step
16.9 x 6.38 x 3.74 mm

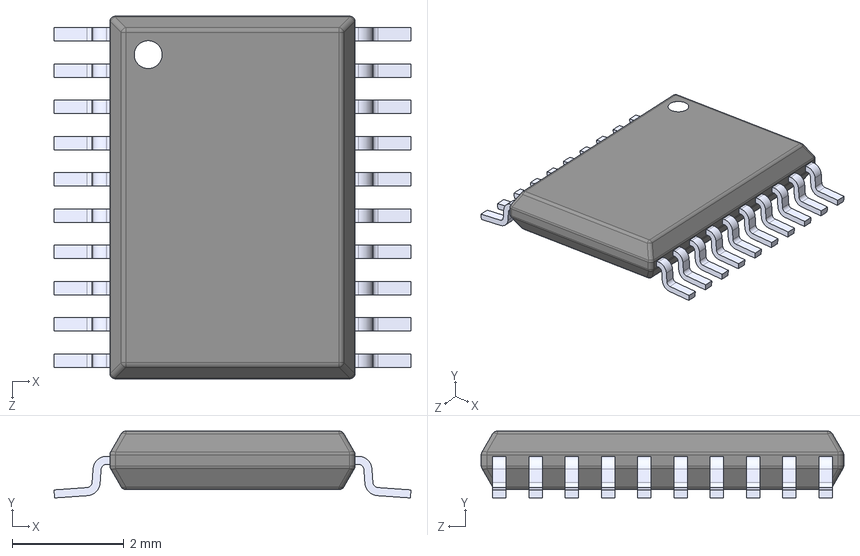
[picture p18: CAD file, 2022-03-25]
parts/3DModels/AD5675/SOP65P640X120-20N.step
6.40 x 1.20 x 6.50 mm

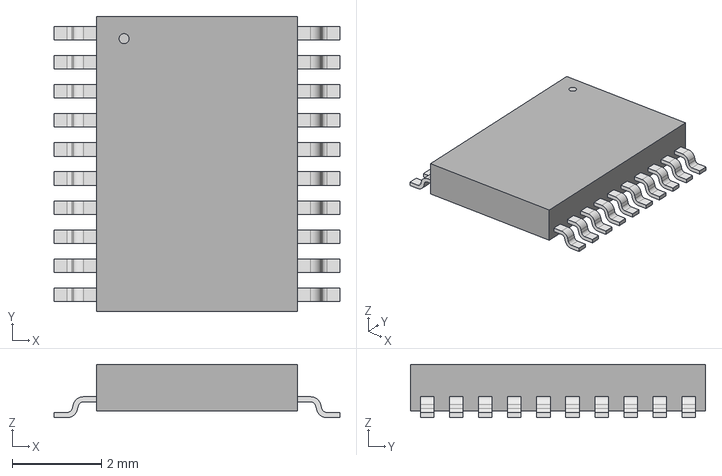
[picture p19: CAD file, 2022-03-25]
parts/3DModels/AD709/RU_20_ADI.step
6.40 x 6.60 x 1.20 mm

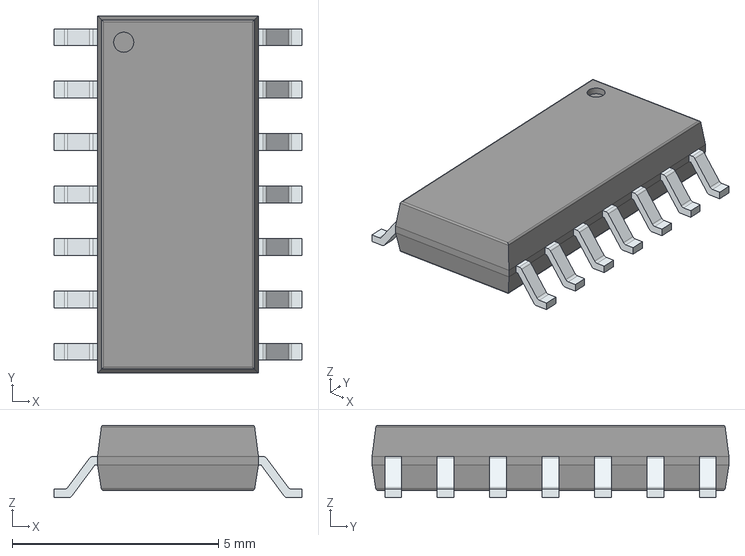
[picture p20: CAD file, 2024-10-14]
parts/3DModels/AD8630WARZ-R7/AD8630WARZ-R7.step
6.00 x 8.65 x 1.75 mm
PinsArrayLR

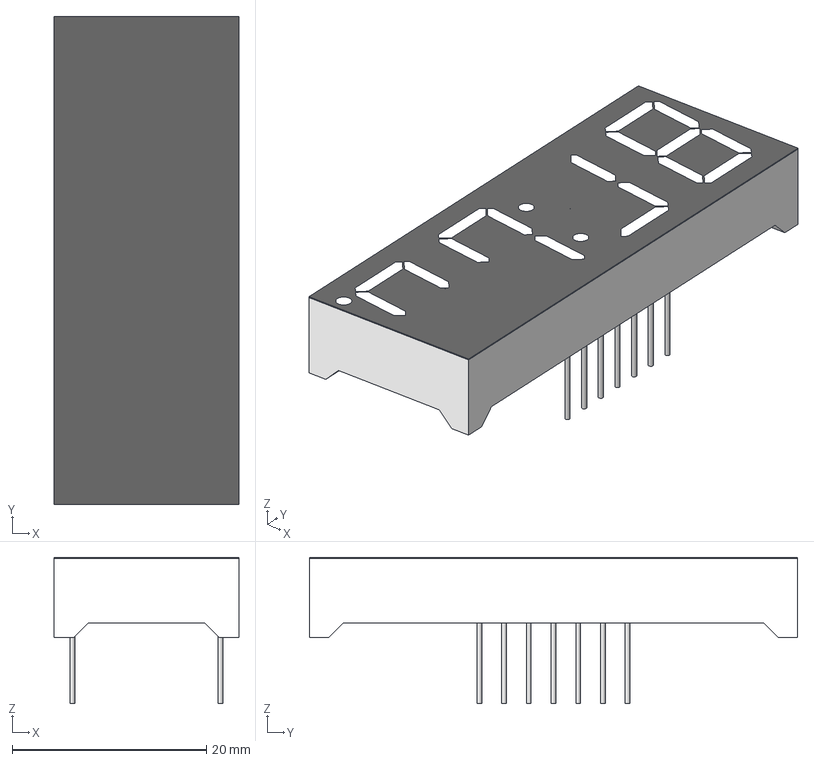
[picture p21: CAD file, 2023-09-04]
parts/3DModels/adafruit_1001/Adafruit_-_1001.step
19.0 x 50.2 x 15.1 mm
top_
pins

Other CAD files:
parts/3DModels/Ampseal-14-RA/1-776266-1.step
parts/3DModels/Ampseal-14/AmpSeal-14.step
parts/3DModels/Ampseal-23/Ampseal_23.step
parts/3DModels/Ampseal-35/C-1-776231-4.step
parts/3DModels/100SP1T1B4M2QE.step
parts/3DModels/3352E.stp
parts/3DModels/3pin-jumper/m20-9990346_asm.stp
parts/3DModels/430452400.stp
parts/3DModels/436450200.stp
parts/3DModels/436500201.stp
parts/3DModels/7461115.stp
parts/3DModels/Ampseal-23-RA/776087-1.step
parts/3DModels/Ampseal-35/ampseal35-otherend.stp
parts/3DModels/Ampseal-8-RA/1-776279-1.step
parts/3DModels/Ampseal-8/1-776276-1.step
parts/3DModels/Atmega16m1/Atmega16m1.step
parts/3DModels/AxialFuse/fuse.STEP
parts/3DModels/B3U_1000P/B3U-1000P.STEP
parts/3DModels/BBS-126-G-A/BBS-126-G-A.stp
parts/3DModels/Barrel_Jack/CUI_DEVICES_PJ-037A.step
parts/3DModels/CAN_Transceiver/SOIC8-N_MC.step
parts/3DModels/CD4044BDR/CD4044BDR.stp
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

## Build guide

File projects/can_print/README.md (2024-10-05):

# can print

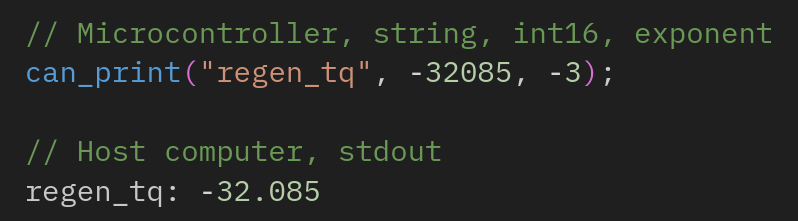
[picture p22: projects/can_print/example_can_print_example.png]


`can print` is a tool for print-based debugging over CAN. All static inputs of a
`can_print` message are processed at _compile time_ using C function-like
macros. Accordingly, an initial configuration of `can_print` with a single print
message adds approximately 400B to an image, and each additional instance of a
message adds 20B. `can_print` messages are set as the lowest priority of
standard 11-bit arbitration IDs via the `0x7FF` ID.

See **Quick Start** to add `can_print` to your project, **Flash and Print
Integration** for running the `can print` decoder after flashing, **Reference**
for using the main `can_print` macro, **Examples** for examples, and **Errata**
for known undefined behavior.

## Quick Start

First, add the `can print` header to a source file and use the `can print`
macro.

```
// example_file.c

// Example usage
#include "projects/can_print/can_print.h"
can_print("regen_tq", -32085, 3);
```

Next, add `can print` as a dependency to the `cc_firmware` rule in your `BUILD`
file.

```
# BUILD
cc_firmware(
    name = "can_print_example",
    srcs = [
        "can_print_example.c",
    ],
    target_compatible_with = select({
        "//bazel/constraints:atmega16m1": [],
        "//conditions:default": ["//bazel/constraints:incompatible_mcu"],
    }),
    deps = [
        ":can_api",
        "//libs/timer",
        "//projects/can_print,
    ],
)
```

Then, start a socketcan connection and the `can_print` decoder. Note that the
decoder is blocking - run it in a new terminal.

```
sudo ip link set can0 up type can bitrate 500000
bazel run //projects/can_print:can_print_decode
```

Finally, flash the target. `can print` output will display as soon as the target
is flashed. The decoder can be kept open between consecutive flashes.

```
bazel run --config=16m1 -c opt //examples/can_print:can_print_example -- -c usbasp
```

### Flash and Print Integration

Through Bazel integrations, `can print` also supports flashing and printing in a
single Bazel command. However, objectively it does not use Bazel properly. Use
at your own risk.

First, add the following parameters to the `cc_firmware` rule in the target
BUILD file.

```
can_print_bitrate = "500000",
can_print_bus = "can0",
can_print_flash_isp = "usbasp",
```

Full `cc_firmware` definition:

```
# BUILD
cc_firmware(
    name = "can_print_example",
    srcs = [
        "can_print_example.c",
    ],
    can_print_bitrate = "500000",
    can_print_bus = "can0",
    can_print_flash_isp = "usbasp",
    target_compatible_with = select({
        "//bazel/constraints:atmega16m1": [],
        "//conditions:default": ["//bazel/constraints:incompatible_mcu"],
    }),
    deps = [
        ":can_api",
        "//libs/timer",
        "//projects/can_print",
    ],
)
```

Then, start a socketcan connection and run the following command:

```
bazel run --config=16m1 -c opt //examples/can_print:can_print
```

For any valid `cc_firmware` instance in a `BUILD` file, the `can_print` target
is available. This target will build an image, flash, and start the decoder in a
single Bazel command.

## Reference

### can print Macro

Main `can_print` macro reference.

`can_print(string, value, multiplier);`

`string`: (char[8]) The string to print. \
`value`: (int16) Optional, the value to print.  
`multiplier`: (int4) Optional, the power of ten to multiply the value by.

### can print Decoder

`can print` decoder reference. Both the bus and bitrate are configurable via
input arguments to the decoder.

```
bazel run //projects/can_print:can_print_decode -- <bus> <bitrate>

# Example
bazel run //projects/can_print:can_print_decode -- can1 250000
```

### Custom Arb ID

The default arb ID used by `can print`, but can be changed to any 11-bit value.
To change the ID, edit the following two files:

```
//projects/can_print/can_print.yml:4
id: 0x7ff
```

```
//projects/can_print/can_print.py:192
ARB_ID = 0x7FF
```

## Examples

The following examples are available in
`//examples/can_print/can_print_example.c`

Example 1: Printing text only

```
can_print("oem");
stdout: oem
```

Example 2: Printing text and a number

```
can_print("oem_num", 240);
stdout: oem_num: 240
```

Example 3: Printing text and a negative number

```
can_print("negative", -12345);
stdout: negative: -12345
```

Example 4: Printing text, a number, and a multiplier

```
can_print("oem_num", 24, 1);
stdout: oem: 240
```

Example 5: Printing text, a number, and a negative multiplier

```
can_print("pi", 31415, -4);
stdout: pi: 3.1415
```

Example 6: Printing text, a negative number, and a negative multiplier

```
can_print("regen_tq", -32085, -3);
stdout: regen_tq: -32.085
```

Example 7: Math in value field, rounded to an int

```
can_print("math", ((3340 + 189) / 2) * 0.25);
stdout: math: 441
```

Example 8: Dynamic values

```
uint16_t counter = 0;
  while (counter < 10) {
      can_print("dynamic",
                counter);
      counter++;
  }

stdout:
dynamic: 0
dynamic: 1 ... dynamic: 9
```

Example 9: Dynamic negative values

```
while (counter > 0) {
    can_print("_dynamic",
              -1 * counter);
    counter--;
}

stdout:
_dynamic: -10
_dynamic: -9 ... _dynamic: -1
```

The next few examples demonstrate unintended uses of `can print`.

Example 10: Character overflow; truncated to 8 characters.

```
can_print("olinelectricmotorsports");
stdout: olinelec
```

Example 11: Value integer overflow; compiler warning

```
can_print("overflow", INT16_MAX + 1);
```

Example 12: Multiplier integer overflow; undefined behavior

```
can_print("multi_ov", 1, 9);
stdout: multi_ov: 1e-07
```

## Errata

Because `value` and `multiplier` can be dynamic values - those unknown at
compile time, there is the risk of integer overflow or underflow. Adding bounds
checking to these values is possible, but would add additional overhead to every
`can print` call. As such, bounds checking is left to the user. The following
known undefined behavior exists:

- Integer overflow and underflow of `value` fails to compile with a static
  value, but prints a unknown value with dynamic values.
- Integer overflow and underflow of `multiplier` compiles, but prints an unknown
  value.

### Future Extentions

The following are future exentions that could either enhance `can print` or
replace it entirely.

- Optional timestamps for can print messages in stdout. Ex: "[2024-09-30
  04:11:13] regen_tq: -32.085"
- Clean up automatic Bazel flash-and-print integration, through parameter
  definition in a global config file.
- Support for floating point and values larger than an `int16`.
- Larger `can_print` messages that stream over multiple CAN messages, adjusting
  to the character and value inputs.
- A wrapper around the `uart` library or modifications to the `uart` library for
  printing over `uart`. This would require the `uart` pins on microcontrollers
  are both reserved and exposed via headers.

## Addendum: can print Bit Packing

A single `can print` message is packed into a standard CAN message of 8 bytes.
The following is pulled directly from `can_print.h`.

```
// can_print.h
/**
- Bit packing for a can print message.
-
-       lsb                                                           msb
- field: |c_0|c_1| c_2 | c_3 | c_4 | c_5 | c_6 | c_7 |value|multi|resv |
- bits: |0-4|5-9|10-14|15-19|20-24|25-29|30-34|35-39|40-55|56-59|60-63|
-
- c_x: An [a-z] character to print.
- int16: A int16 value to print.
- multi: The multiplier to apply to the value.
- resv: Reserved bits. Do not access.
*/
```

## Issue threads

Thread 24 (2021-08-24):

Create github action for verifying new OEM parts additions

coreyacl, 2021-08-24:
Kicad files are written in plaintext which means we can check to see if a new symbol has the appropriate fields with a simple script. We can even check if the associated footprint has a 3D model, and if that 3D model is linked correctly using kicad aliases.

jack-greenberg, 2021-08-25:
A good resource explaining how KiCad files are constructed: https://en.wikibooks.org/wiki/Kicad/file_formats#Schematic_Libraries_Files_Format

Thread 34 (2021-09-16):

Add in KiCad CI Actions

jack-greenberg, 2021-09-16:
## Ideas

* If there is a `*-rescue.lib` file, CI should fail
* Autogenerate BOMs, GERBERs, DXFs, and automatically upload them somewhere? Outline? Google Drive?

jack-greenberg, 2021-09-16:
https://github.com/INTI-CMNB/KiBot#usage-of-github-actions

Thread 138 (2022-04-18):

Fan PWM support for BMS

jack-greenberg, 2022-04-18:
Currently the fan PWM doesn't work on the BMS. Some config needs to change in `bms_config.h` and possibly in `temperature_task.c`.

Closed 2024-03-20.

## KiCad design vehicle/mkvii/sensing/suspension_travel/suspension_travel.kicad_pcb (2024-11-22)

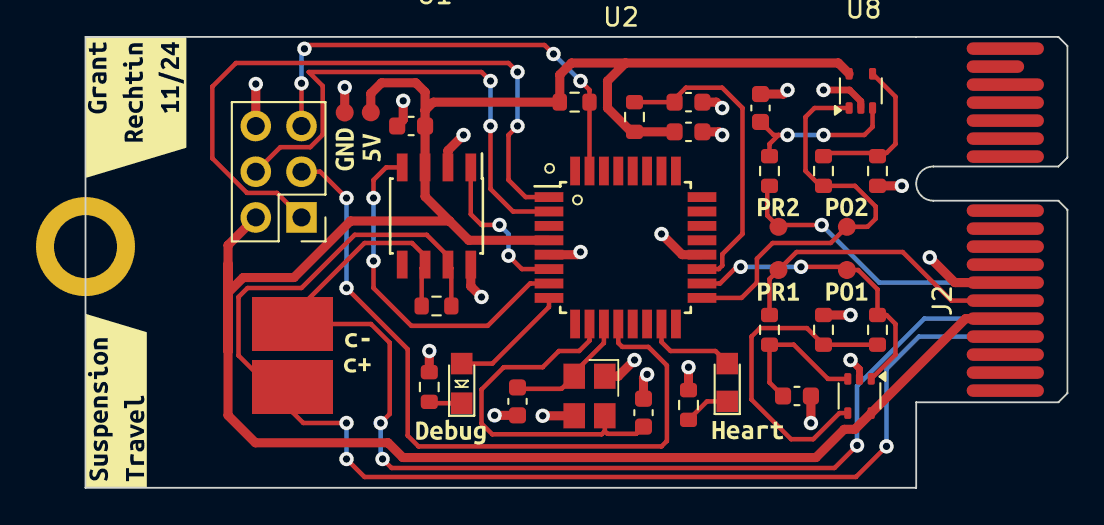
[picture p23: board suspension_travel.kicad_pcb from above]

Board: 2 copper layers, 54.6 x 25.0 mm, 48 parts (0 on the bottom side), 25 nets.

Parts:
5VTestPoint1: TestPoint; TestPoint_Pad_D1mm
C1, C3, C6, C7: C_0.1uF; C_0603
C2: C_100pF; C_0603
C4, C5: C_30pF; C_0603
Can+Tp1: TestPoint; Test_Point_SMD
Can-TP1: TestPoint; Test_Point_SMD
D1: LED_0805; LED_0805_OEM
D2: LED_AMBER; CHIPLED_0805
GND1: TestPoint; TestPoint_Pad_D1mm
H1: CONN_MountingHole; PCIe_Mount
J1: CONN_02X03; PinHeader_2x03_P2.54mm_Vertical
J2: CONN_pcie_x1; pcie_x1
LP1_POST1, LP1_PRE1, LP2_POST1, LP2_PRE1: TestPoint; TestPoint_Pad_D1mm
R1, R4, R5, R6, R9, R10: R_100; R_0603
R2: R_120_DNP; R_0603
R3: R_10K; R_0603
R7, R8: R_200; R_0603
R11: R_1K; R_0603
U1: MCP2561-E_SN; SOIC-8_3.9x4.9mm_Pitch1.27mm_OEM
U2: ATMEGA16M1; TQFP-32_7x7mm_Pitch0.8mm
U3, U8: U_OPAMP_MCP6001; SOT-353_SC-70-5
Y1: Crystal_SMD; Crystal_TXC7M
kibuzzard-673FD6A4: G***; kibuzzard-673FD6A4
kibuzzard-673FD6B3: G***; kibuzzard-673FD6B3
kibuzzard-673FD6DC: G***; kibuzzard-673FD6DC
kibuzzard-673FD6EA: G***; kibuzzard-673FD6EA
kibuzzard-673FD6F4: G***; kibuzzard-673FD6F4
kibuzzard-673FD70C: G***; kibuzzard-673FD70C
kibuzzard-673FD675: G***; kibuzzard-673FD675
kibuzzard-673FD704: G***; kibuzzard-673FD704
kibuzzard-673FD725: G***; kibuzzard-673FD725
kibuzzard-673FD744: G***; kibuzzard-673FD744
kibuzzard-6740EEA9: G***; kibuzzard-6740EEA9
kibuzzard-6740EF04: G***; kibuzzard-6740EF04

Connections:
+5V: 5VTestPoint1.1, C1.1, C3.1, J1.2, J2.B5 (5V), R1.1, R3.1, U1.3 (VDD), U2.4 (VCC), U3.5 (V+), U8.5 (V+)
/CAN_+: Can+Tp1.1, J2.A4 (CAN+), R2.1, U1.7 (CANH)
/CAN_-: Can-TP1.1, J2.A5 (CAN-), R2.2, U1.6 (CANL)
/CAN_RX: U1.4 (RXD), U2.7 ((PCINT11/T1/ICP1B/RXCAN)PC3)
/CAN_TX: U1.1 (TXD), U2.6 ((PCINT10/T0/TXCAN)PC2)
/DEBUG_LED: D1.2 (A), U2.8 ((PCINT0/MISO/PSCOUT2A)PB0)
/Heartbeat: D2.2 (A), U2.15 ((PCINT23/ACMP0)PD7)
/MISO: J1.1, U2.1 ((PCINT18/PSCIN2/OC1A/MISO_A)PD2)
/MOSI: J1.4, U2.2 ((PCINT19/TXD/TXLIN/OC0A/~SS/MOSI_A)PD3)
/RESET: J1.5, R3.2, U2.31 ((PCINT24/OCD/~RESET)PE0)
/SCK: J1.3, U2.12 ((PCINT20/ADC1/RXD/RXLIN/ICP1A/SCK_A)PD4)
/lp1_Vout: J2.B6 (io_1), LP1_PRE1.1, R5.1
/lp1_fVout: LP1_POST1.1, R9.1, U2.18 ((PCINT13/ADC9/ACMP3/AMP1+)PC5), U3.1
/lp2_Vout: J2.A7 (io_2), LP2_PRE1.1, R6.1
/lp2_fVout: LP2_POST1.1, R10.1, U2.17 ((PCINT12/ADC8/ACMPN3/AMP1-)PC4), U8.1
GND: C1.2, C2.2, C3.2, C4.2, C5.2, C6.2, C7.2, GND1.1, H1.1, J1.6, J2.A3 (GND), J2.A6 (io_0), J2.B4 (GND), J2.B7 (io_3), R4.2, R7.1, R8.1, R11.2, U1.2 (VSS), U1.8 (STBY), U2.5 (GND), U2.20 (AGND), U3.2 (V-), U8.2 (V-), Y1.2, Y1.4
unnamed: D1.1 (K), R4.1
unnamed: D2.1 (K), R11.1
unnamed: C5.1, U2.10 ((PCINT25/OC0B/XTAL1)PE1), Y1.3
unnamed: C4.1, U2.11 ((PCINT26/ADC0/XTAL2)PE2), Y1.1
unnamed: C2.1, R1.2, U2.19 (AVCC)
unnamed: C6.1, R5.2, U3.3 (+)
unnamed: R7.2, R9.2, U3.4 (-)
unnamed: C7.1, R6.2, U8.3 (+)
unnamed: R8.2, R10.2, U8.4 (-)

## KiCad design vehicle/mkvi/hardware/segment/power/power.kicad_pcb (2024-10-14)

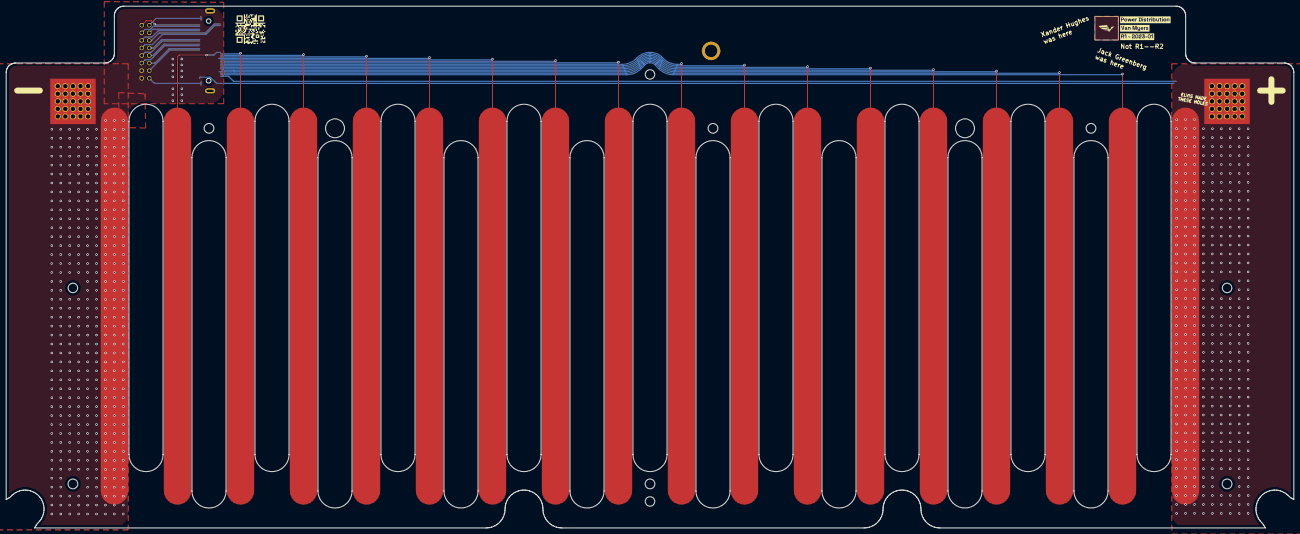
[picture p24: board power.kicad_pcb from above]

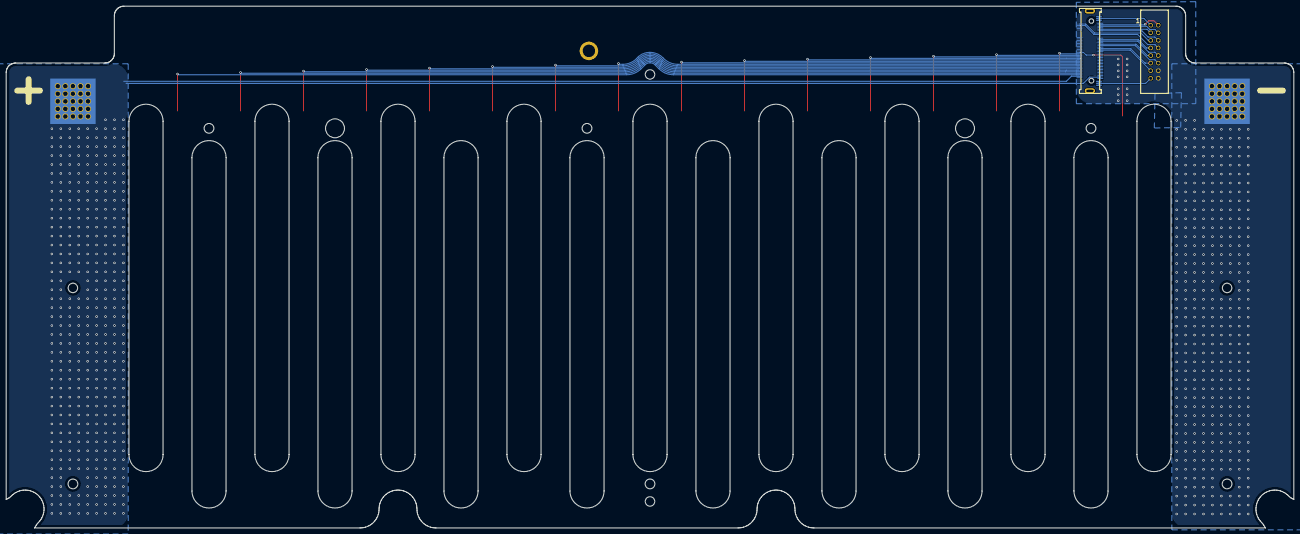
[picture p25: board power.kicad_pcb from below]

Board: 4 copper layers, 431.8 x 175.0 mm, 26 parts (4 on the bottom side), 32 nets.

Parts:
J1: Automotive_M.2; MKVI_BMS_CSC
J2: TST-108-01-T-D; TST-108-XX-T-D
QR*****: hw.oem.to/6_PD_1; QR_6_PD_1
TP1, TP2, TP3, TP4, TP5, TP6, TP7, TP8, TP9, TP10, TP11, TP12, TP13, TP14, TP15, TP16, TP17, TP18: TestPoint; Bond Pad
TP19, TP20: TestPoint; Wurth-7461115
kibuzzard-63B8B2B4: G***; kibuzzard-63B8B2B4
kibuzzard-63B8B2E9: G***; kibuzzard-63B8B2E9
kibuzzard-63BE1F6F: G***; kibuzzard-63BE1F6F

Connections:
/CELL1: J1.56, TP1.1
/CELL2: J1.57, TP2.1
/CELL3: J1.58, TP3.1
/CELL4: J1.59, TP4.1
/CELL5: J1.60, TP5.1
/CELL6: J1.61, TP6.1
/CELL7: J1.62, TP7.1
/CELL8: J1.63, TP8.1
/CELL9: J1.64, TP9.1
/CELL10: J1.65, TP10.1
/CELL11: J1.66, TP11.1
/CELL12: J1.67, TP12.1
/CELL13: J1.68, TP13.1
/CELL14: J1.69, TP14.1
/CELL15: J1.70, TP15.1
/CELL16: J1.71, TP16.1
/CELL17: J1.36, J1.37, J1.72, TP17.1, TP20.1
/MUX1_SC: J1.17, J2.11
/MUX1_SD: J1.18, J2.13
/MUX2_SC: J1.14, J2.9
/MUX2_SD: J1.15, J2.12
/MUX3_SC: J1.11, J2.7
/MUX3_SD: J1.12, J2.10
/MUX4_SC: J1.8, J2.3
/MUX4_SD: J1.9, J2.6
/MUX_OUT_1: J1.6, J2.4
/MUX_OUT_2: J1.42, J2.8
/MUX_OUT_3: J1.5, J2.2
/MUX_OUT_4: J1.41, J2.5
/VREF2: J1.P38, J1.P39, J1.P40, J2.15
/VREG: J1.P1, J1.P2, J1.P3, J2.1
GND: J1.4, J1.7, J1.10, J1.13, J1.16, J1.19, J1.43, J1.46, J2.14, J2.16, TP18.1, TP19.1

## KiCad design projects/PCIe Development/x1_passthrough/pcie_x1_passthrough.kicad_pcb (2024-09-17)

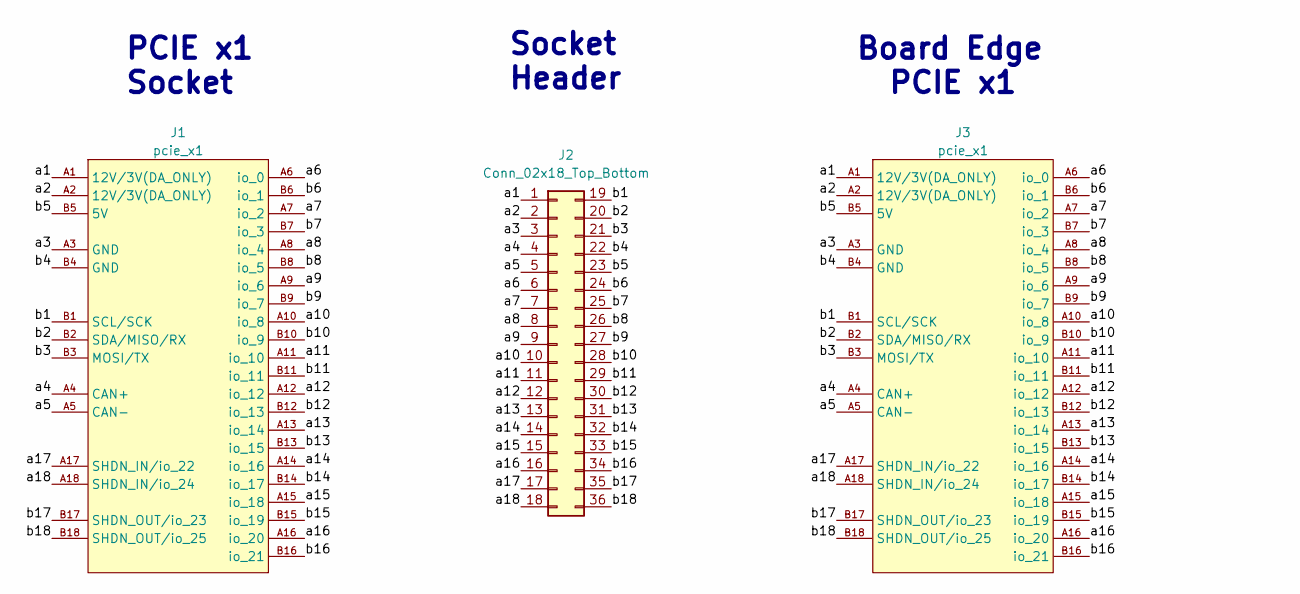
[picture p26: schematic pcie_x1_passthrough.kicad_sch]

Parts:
J1: pcie_x1; te_pcie_x1_connector
J2: Conn_02x18_Top_Bottom; PinSocket_2x18_P2.54mm_Vertical
J3: pcie_x1

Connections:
/a1: J1.A1 (12V/3V(DA_ONLY)), J2.1, J3.A1 (12V/3V(DA_ONLY))
/a2: J1.A2 (12V/3V(DA_ONLY)), J2.2, J3.A2 (12V/3V(DA_ONLY))
/a3: J1.A3 (GND), J2.3, J3.A3 (GND)
/a4: J1.A4 (CAN+), J2.4, J3.A4 (CAN+)
/a5: J1.A5 (CAN-), J2.5, J3.A5 (CAN-)
/a6: J1.A6 (io_0), J2.6, J3.A6 (io_0)
/a7: J1.A7 (io_2), J2.7, J3.A7 (io_2)
/a8: J1.A8 (io_4), J2.8, J3.A8 (io_4)
/a9: J1.A9 (io_6), J2.9, J3.A9 (io_6)
/a10: J1.A10 (io_8), J2.10, J3.A10 (io_8)
/a11: J1.A11 (io_10), J2.11, J3.A11 (io_10)
/a12: J1.A12 (io_12), J2.12, J3.A12 (io_12)
/a13: J1.A13 (io_14), J2.13, J3.A13 (io_14)
/a14: J1.A14 (io_16), J2.14, J3.A14 (io_16)
/a15: J1.A15 (io_18), J2.15, J3.A15 (io_18)
/a16: J1.A16 (io_20), J2.16, J3.A16 (io_20)
/a17: J1.A17 (SHDN_IN/io_22), J2.17, J3.A17 (SHDN_IN/io_22)
/a18: J1.A18 (SHDN_IN/io_24), J2.18, J3.A18 (SHDN_IN/io_24)
/b1: J1.B1 (SCL/SCK), J2.19, J3.B1 (SCL/SCK)
/b2: J1.B2 (SDA/MISO/RX), J2.20, J3.B2 (SDA/MISO/RX)
/b3: J1.B3 (MOSI/TX), J2.21, J3.B3 (MOSI/TX)
/b4: J1.B4 (GND), J2.22, J3.B4 (GND)
/b5: J1.B5 (5V), J2.23, J3.B5 (5V)
/b6: J1.B6 (io_1), J2.24, J3.B6 (io_1)
/b7: J1.B7 (io_3), J2.25, J3.B7 (io_3)
/b8: J1.B8 (io_5), J2.26, J3.B8 (io_5)
/b9: J1.B9 (io_7), J2.27, J3.B9 (io_7)
/b10: J1.B10 (io_9), J2.28, J3.B10 (io_9)
/b11: J1.B11 (io_11), J2.29, J3.B11 (io_11)
/b12: J1.B12 (io_13), J2.30, J3.B12 (io_13)
/b13: J1.B13 (io_15), J2.31, J3.B13 (io_15)
/b14: J1.B14 (io_17), J2.32, J3.B14 (io_17)
/b15: J1.B15 (io_19), J2.33, J3.B15 (io_19)
/b16: J1.B16 (io_21), J2.34, J3.B16 (io_21)
/b17: J1.B17 (SHDN_OUT/io_23), J2.35, J3.B17 (SHDN_OUT/io_23)
/b18: J1.B18 (SHDN_OUT/io_25), J2.36, J3.B18 (SHDN_OUT/io_25)

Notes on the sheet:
Socket Header
Board Edge PCIE x1
PCIE x1 Socket

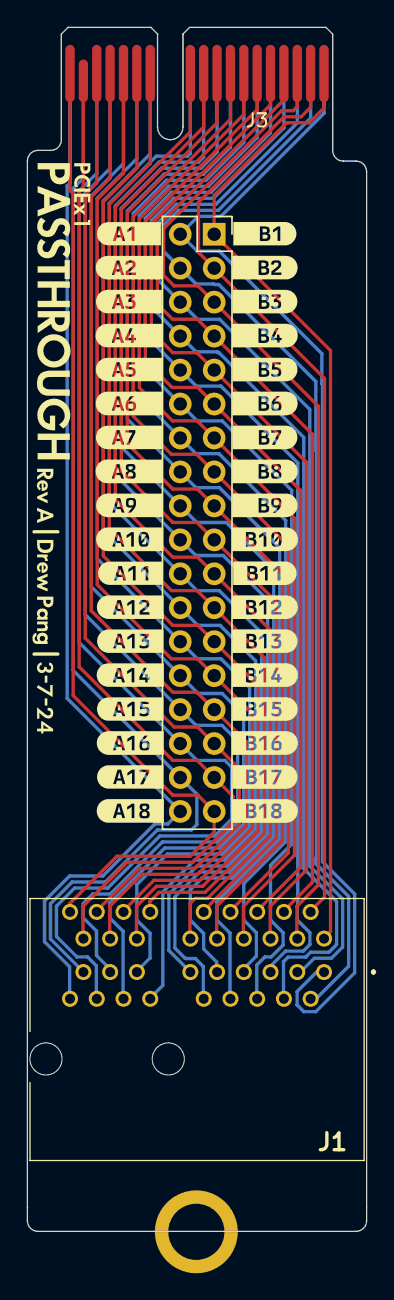
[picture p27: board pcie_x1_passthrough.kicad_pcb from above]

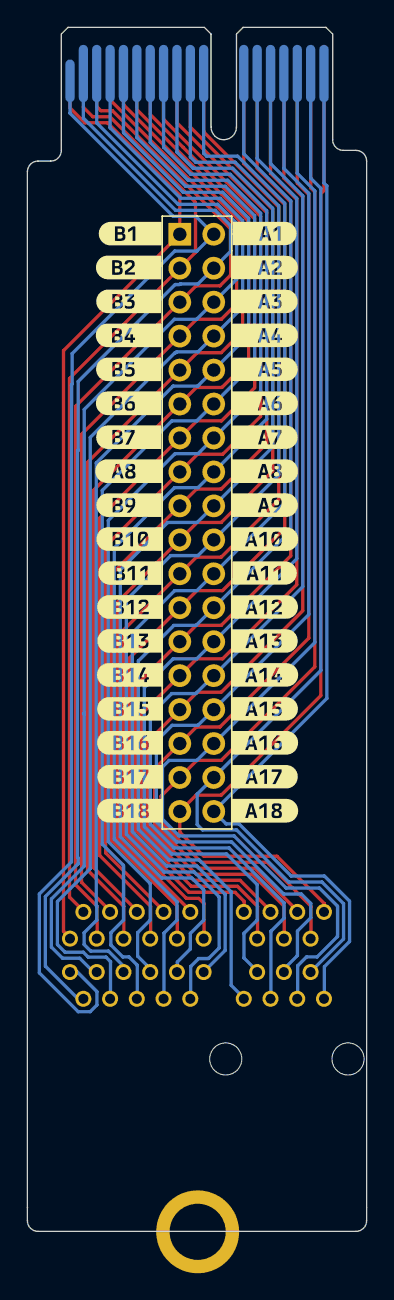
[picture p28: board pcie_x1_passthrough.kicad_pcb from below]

Board: 2 copper layers, 25.4 x 90.1 mm, 79 parts (37 on the bottom side), 36 nets.

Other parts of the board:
J2#2: Conn_02x18_Top_Bottom; PinSocket_2x18_P2.54mm_Vertical
kibuzzard-65E95D19: G***; kibuzzard-65E95D19
kibuzzard-65E95DA8: G***; kibuzzard-65E95DA8
kibuzzard-65E95DDF, kibuzzard-65E95DDF#2: G***; kibuzzard-65E95DDF
kibuzzard-65E95DE4: G***; kibuzzard-65E95DE4
kibuzzard-65E95DEB: G***; kibuzzard-65E95DEB
kibuzzard-65E95DEF: G***; kibuzzard-65E95DEF
kibuzzard-65E95DF3: G***; kibuzzard-65E95DF3
kibuzzard-65E95DF8: G***; kibuzzard-65E95DF8
kibuzzard-65E95DFB: G***; kibuzzard-65E95DFB
kibuzzard-65E95E04: G***; kibuzzard-65E95E04
kibuzzard-65E95E8F: G***; kibuzzard-65E95E8F
kibuzzard-65E95E9B: G***; kibuzzard-65E95E9B
kibuzzard-65E95E9E: G***; kibuzzard-65E95E9E
kibuzzard-65E95E93: G***; kibuzzard-65E95E93
kibuzzard-65E95E97: G***; kibuzzard-65E95E97
kibuzzard-65E95EA2: G***; kibuzzard-65E95EA2
kibuzzard-65E95EA8: G***; kibuzzard-65E95EA8
kibuzzard-65E95EAD: G***; kibuzzard-65E95EAD
kibuzzard-65E95F03: G***; kibuzzard-65E95F03
kibuzzard-65E960EE: G***; kibuzzard-65E960EE
kibuzzard-65E962FB: G***; kibuzzard-65E962FB
kibuzzard-65E962FE: G***; kibuzzard-65E962FE
kibuzzard-65E963A3: G***; kibuzzard-65E963A3
kibuzzard-65E963A9: G***; kibuzzard-65E963A9
kibuzzard-65E963AE: G***; kibuzzard-65E963AE
kibuzzard-65E969A0: G***; kibuzzard-65E969A0
kibuzzard-65E969A4: G***; kibuzzard-65E969A4
kibuzzard-65E969AA: G***; kibuzzard-65E969AA
kibuzzard-65E969AE: G***; kibuzzard-65E969AE
kibuzzard-65E969B1: G***; kibuzzard-65E969B1
kibuzzard-65E969B6: G***; kibuzzard-65E969B6
kibuzzard-65E969BA: G***; kibuzzard-65E969BA
kibuzzard-65E969BF: G***; kibuzzard-65E969BF
kibuzzard-65E969C2: G***; kibuzzard-65E969C2
kibuzzard-65E969C6: G***; kibuzzard-65E969C6
kibuzzard-65E969CA: G***; kibuzzard-65E969CA
kibuzzard-65E969CE: G***; kibuzzard-65E969CE
kibuzzard-65E969D2: G***; kibuzzard-65E969D2
kibuzzard-65E969D5: G***; kibuzzard-65E969D5
kibuzzard-65E969DA: G***; kibuzzard-65E969DA
kibuzzard-65E969DD: G***; kibuzzard-65E969DD
kibuzzard-65E969E1: G***; kibuzzard-65E969E1
kibuzzard-65E969E5: G***; kibuzzard-65E969E5
kibuzzard-65E969E9: G***; kibuzzard-65E969E9
kibuzzard-65E969ED: G***; kibuzzard-65E969ED
kibuzzard-65E9630A: G***; kibuzzard-65E9630A
kibuzzard-65E9633C: G***; kibuzzard-65E9633C
kibuzzard-65E9636C: G***; kibuzzard-65E9636C
kibuzzard-65E9638D: G***; kibuzzard-65E9638D
kibuzzard-65E9639B: G***; kibuzzard-65E9639B
kibuzzard-65E9639F: G***; kibuzzard-65E9639F
kibuzzard-65E9696D: G***; kibuzzard-65E9696D
kibuzzard-65E9697B: G***; kibuzzard-65E9697B
kibuzzard-65E9698D: G***; kibuzzard-65E9698D
kibuzzard-65E9699C: G***; kibuzzard-65E9699C
kibuzzard-65E96100: G***; kibuzzard-65E96100
kibuzzard-65E96303: G***; kibuzzard-65E96303
kibuzzard-65E96310: G***; kibuzzard-65E96310
kibuzzard-65E96314: G***; kibuzzard-65E96314
kibuzzard-65E96318: G***; kibuzzard-65E96318
kibuzzard-65E96322: G***; kibuzzard-65E96322
kibuzzard-65E96383: G***; kibuzzard-65E96383
kibuzzard-65E96396: G***; kibuzzard-65E96396
kibuzzard-65E96959: G***; kibuzzard-65E96959
kibuzzard-65E96962: G***; kibuzzard-65E96962
kibuzzard-65E96967: G***; kibuzzard-65E96967
kibuzzard-65E96973: G***; kibuzzard-65E96973
kibuzzard-65E96977: G***; kibuzzard-65E96977
kibuzzard-65E96980: G***; kibuzzard-65E96980
kibuzzard-65E96984: G***; kibuzzard-65E96984
kibuzzard-65E96989: G***; kibuzzard-65E96989
kibuzzard-65E96991: G***; kibuzzard-65E96991
kibuzzard-65E96995: G***; kibuzzard-65E96995
kibuzzard-65E96999: G***; kibuzzard-65E96999

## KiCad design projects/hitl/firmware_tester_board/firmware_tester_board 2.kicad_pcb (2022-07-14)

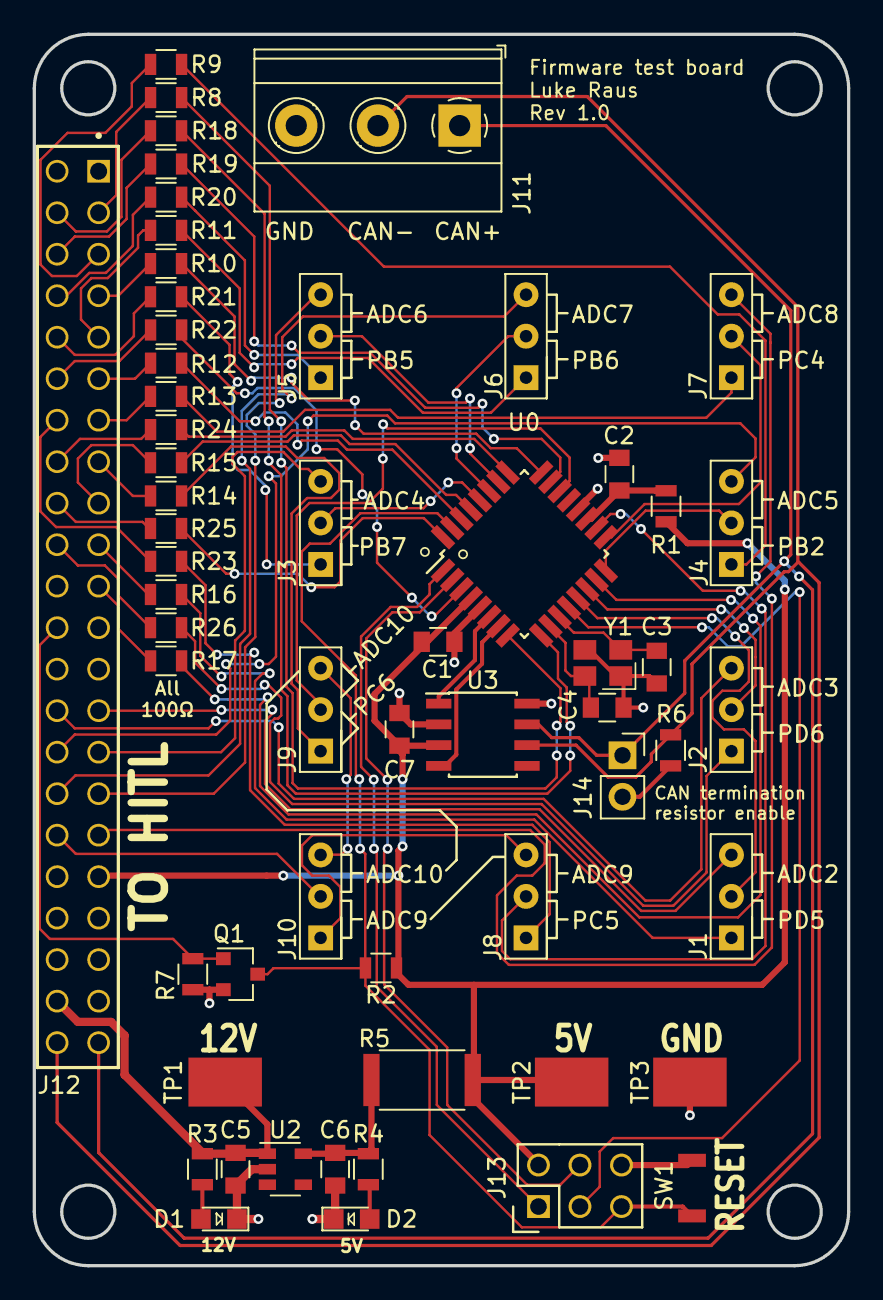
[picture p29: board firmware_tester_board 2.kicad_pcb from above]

Board: 2 copper layers, 49.8 x 75.4 mm, 58 parts (0 on the bottom side), 76 nets.

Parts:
C1, C7: C_0.1uF; C_0805_OEM
C2: C_100pF; C_0805_OEM
C3, C4: C_30pF; C_0805_OEM
C5, C6: C_1uF; C_0805_OEM
D1, D2: LED_0805; LED_0805_OEM
J1, J2, J3, J4, J5, J6, J7, J8, J9, J10: CONN_01X03; PinHeader_1x03_P2.54mm_Vertical
J11: Screw_Terminal_01x03; TerminalBlock_Phoenix_MKDS-1,5-3_1x03_P5.00mm_Horizontal
J12: SSW-122-01-G-D; SAMTEC_SSW-122-01-G-D
J13: CONN_02X03; Pin_Header_Straight_2x03
J14: CONN_01x02; PinSocket_1x02_P2.54mm_Vertical
Q1: SSM3K333R; SOT-23F
R1, R8, R9, R10, R11, R12, R13, R14, R15, R16, R17, R18, R19, R20, R21, R22, R23, R24, R25, R26: R_100; R_0805_OEM
R2, R7: R_10K; R_0805_OEM
R3: R_1K; R_0805_OEM
R4: R_200; R_0805_OEM
R5: R_0_2512; R_2512_OEM
R6: R_120; R_0805_OEM
SW1: SW_Push_SPST_NO; SW_B3U-1000P_4.2x1.7mm
TP1, TP2, TP3: Test_Point_SMD
U0: ATMEGA64M1; TQFP-32_7x7mm_Pitch0.8mm
U2: AP7370; SOT-23-5
U3: MCP2561-E_SN; SOIC-8_3.9x4.9mm_Pitch1.27mm_OEM
Y1: Crystal_SMD; Crystal_SMD_FA238

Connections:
+5V: C1.1, C7.1, J12.35, J13.2, R1.1, R2.1, R5.1, TP2.1, U0.4, U3.3
+12V: C5.1, J12.42, R3.1, TP1.1, U2.1
/ADC2: J1.3, J12.27
/ADC3: J2.3, J12.28
/ADC4: J3.3, J12.29
/ADC5: J4.3, J12.30
/ADC6: J5.3, J12.31
/ADC7: J6.3, J12.32
/ADC8: J7.3, J12.33
/ADC9: J8.3, J10.1
/ADC9_ADC10: J10.2, J12.34
/ADC10: J9.3, J10.3
/CAN_+: J11.1, J12.43, J14.1, U3.7
/CAN_-: J11.2, J12.44, R6.2, U3.6
/CAN_RX: U0.7, U3.4
/CAN_TX: U0.6, U3.1
/DIG-RESET: J12.24, Q1.1, R7.2
/MISO: J13.1, U0.1
/MOSI: J13.4, U0.2
/PB0: R8.1, U0.8
/PB1: R18.2, U0.9
/PB2: J4.1, R9.1
/PB2_ADC5: J4.2, U0.16
/PB3: R19.2, U0.23
/PB4: R10.1, U0.24
/PB5: J5.1, R20.2
/PB5_ADC6: J5.2, U0.26
/PB6: J6.1, R11.1
/PB6_ADC7: J6.2, U0.27
/PB7: J3.1, R21.2
/PB7_ADC4: J3.2, U0.28
/PC0: R12.1, U0.30
/PC1: R22.2, U0.3
/PC4: J7.1, R13.1
/PC4_ADC8: J7.2, U0.17
/PC5: J8.1, R23.2
/PC5_ADC9: J8.2, U0.18
/PC6: J9.1, R14.1
/PC6_ADC10: J9.2, U0.22
/PC7: R24.2, U0.25
/PD0: R15.1, U0.29
/PD1: R25.2, U0.32
/PD5: J1.1, R16.1
/PD5_ADC2: J1.2, U0.13
/PD6: J2.1, R26.2
/PD6_ADC3: J2.2, U0.14
/PD7: R17.1, U0.15
/RESET: J13.5, Q1.3, R2.2, SW1.1, U0.31
/SCK: J13.3, U0.12
GND: C1.2, C2.2, C3.2, C4.2, C5.2, C6.2, C7.2, D1.1, D2.1, J11.3, J12.01, J12.02, J12.25, J12.26, J12.41, J13.6, Q1.2, R7.1, SW1.2, TP3.1, U0.5, U0.20, U2.2, U3.2, U3.8, Y1.2, Y1.4
unnamed: C2.1, R1.2, U0.19
unnamed: C3.1, U0.11, Y1.1
unnamed: C4.1, U0.10, Y1.3
unnamed: C6.1, R4.1, R5.2, U2.5
unnamed: D1.2, R3.2
unnamed: D2.2, R4.2
unnamed: J12.03, R8.2
unnamed: J12.04, R18.1
unnamed: J12.05, R9.2
unnamed: J12.06, R19.1
unnamed: J12.07, R10.2
unnamed: J12.08, R20.1
unnamed: J12.09, R11.2
unnamed: J12.10, R21.1
unnamed: J12.11, R12.2
unnamed: J12.12, R22.1
unnamed: J12.13, R13.2
unnamed: J12.14, R23.1
unnamed: J12.15, R14.2
unnamed: J12.16, R24.1
unnamed: J12.17, R15.2
unnamed: J12.18, R25.1
unnamed: J12.19, R16.2
unnamed: J12.20, R26.1
unnamed: J12.21, R17.2
unnamed: J14.2, R6.1

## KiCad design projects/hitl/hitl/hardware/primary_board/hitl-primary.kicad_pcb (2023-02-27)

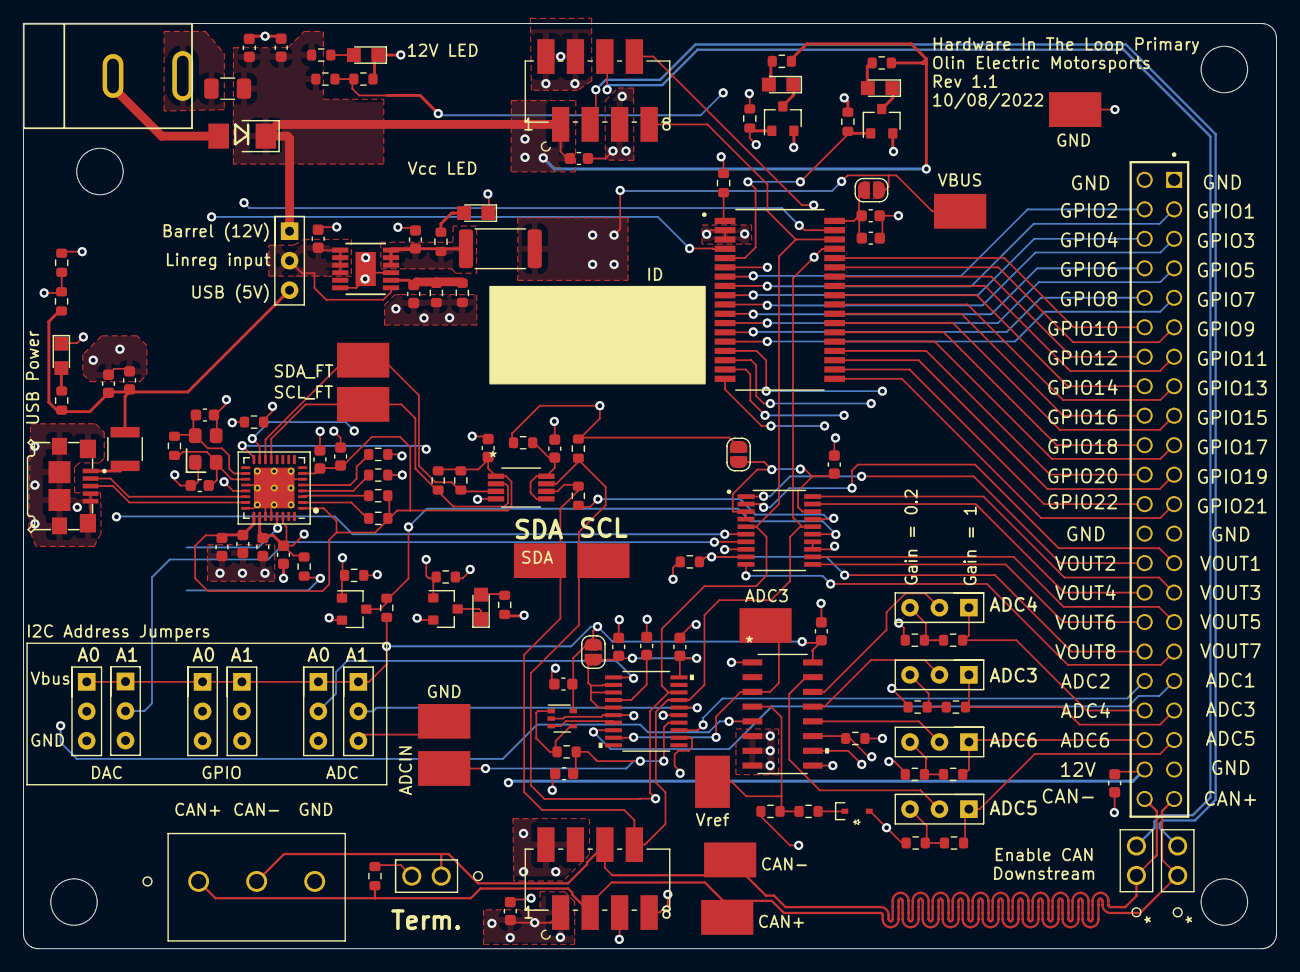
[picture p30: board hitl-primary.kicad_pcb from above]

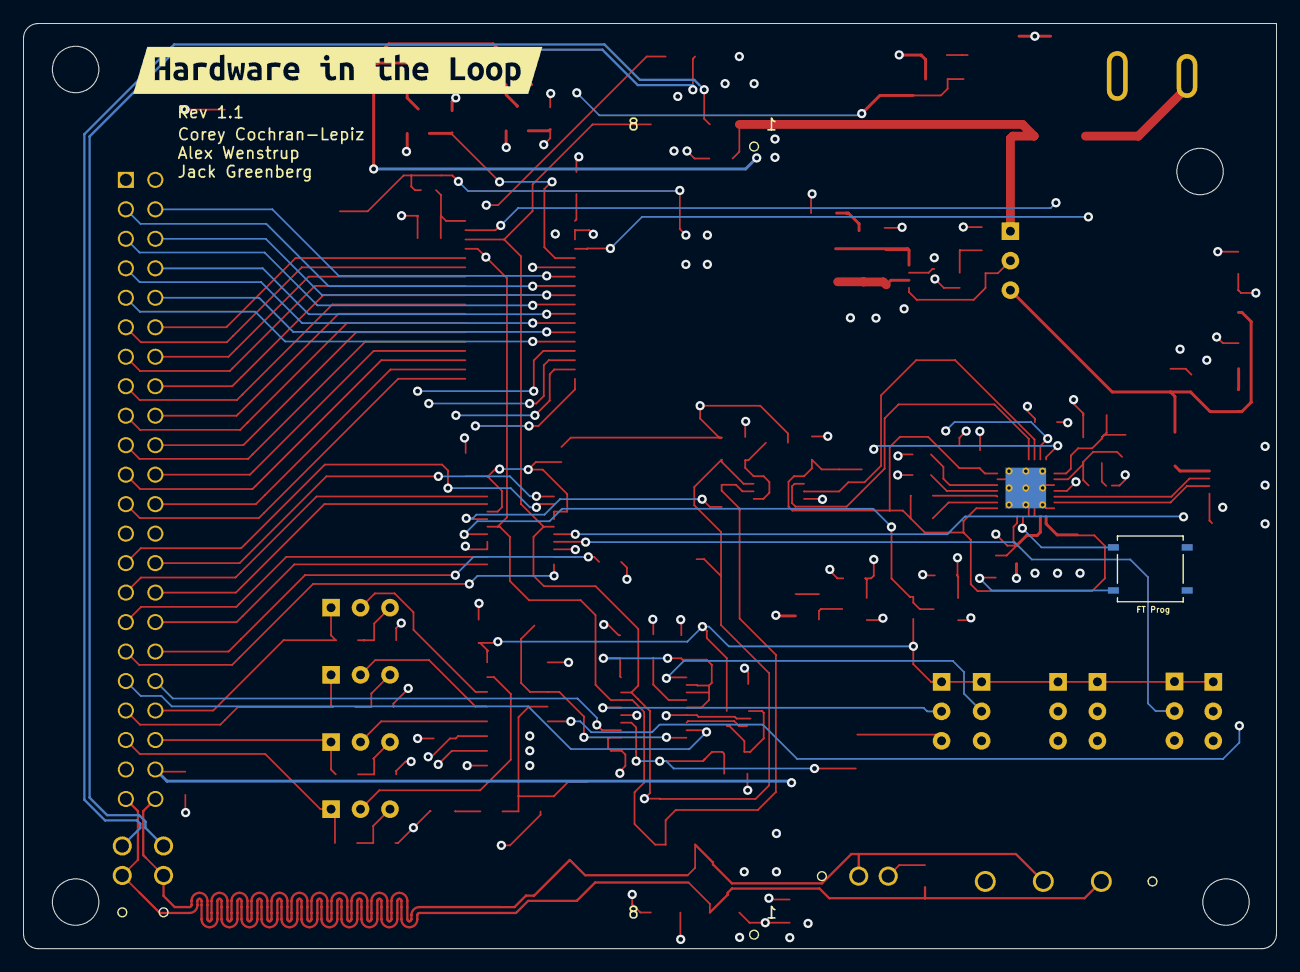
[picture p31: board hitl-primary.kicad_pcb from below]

Board: 4 copper layers, 108.0 x 79.7 mm, 134 parts (2 on the bottom side), 113 nets.

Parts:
C1, C8, C10, C13, C15, C26: 4u7F; C_0603
C2, C9, C11, C14, C16, C18, C25: 0u1F; C_0603
C3, C7, C24: 30pF; C_0603
C4, C5, C6, C12, C17, C19, C20, C27, C29: 10uF_35V; C_0603
C21: 2u2F; C_0603
C22, C23, C28: 1uF; C_0603
D1, D3, D8: LED_WHITE; CHIPLED_0805
D4: LED_BLUE; CHIPLED_0805
D5, D6: LED_ORANGE; CHIPLED_0805
D7: GDZ2V0B-G3-08; SOD-323
D501: SMBJ5355B-TP; DO-214AA
F1: F_500mA_16V; Fuse_1210
F2: F_1500mA_63V; Fuse_1206
J1: USB-Micro-1981568-1; TE_1981568-1
J2: Barrel_Jack; barrel_jack_PJ-037A
J3, J4: CONN_MM_F_VT_08_SM; micromatch_female_vert_8_sm
J6, J13, J15: CONN_01x02; pinheader_1x2
J7, J8, J9, J10, J11, J12, J16, J17, J18, J19, J20: CONN_01X03; PinHeader_1x03_P2.54mm_Vertical
J14: SSW-122-01-G-D; SAMTEC_SSW-122-01-G-D
J21: Screw_Terminal_01x03; ScrewPin_1x3
JP1, JP2, JP3: SolderJumper_2_Open; SolderJumper-2_P1.3mm_Open_RoundedPad1.0x1.5mm
Q1, Q2, Q3, Q4: SSM3K333R; SOT-23F
R1, R6, R8, R32, R34, R36, R38: 12KR; R_0603
R2, R7, R9, R18, R25, R27, R33, R35, R37, R39: 3KR; R_0603
R3, R5, R13, R15, R17, R24, R26, R28, R29, R31: 10KR; R_0603
R4: 1MR; R_0603
R10, R11: 0R; R_0603
R12, R14, R21, R22: 8K06R; R_0603
R16: 120R; R_0603
R19: 100KR; R_0603
R20: 39KR; R_0603
R23, R30, R47, R401: 1KR; R_0603
R40: 33K2R; R_0603
R41: 49K9R; R_0603
R42: 330R; R_0603
R43: 0R_2512; R_2512_6332Metric
SW1: SW_SPST; Button_PTS526
TP1, TP2, TP3, TP4, TP5, TP6, TP7, TP8, TP9, TP10, TP11, TP12: TP_SMD; Test_Point_SMD
U1: PCA9517; Micro8_PCA9517
U2: FT4222H; VQFN-32-1EP_5x5mm_P0.5mm_EP3.5x3.5mm_ThermalVias
U4: AD5675; SOP65P640X120-20N_AD
U5: MAX7300AAXT; SOP80P1030X264-36N
U6: AD7091R-5BRUZ
U7: MCP6001; SOT-353_SC-70-5
U8: 74HCT4051D
U9: LT3045; MSOP-12_MSE
Y1: Crystal_12MHz_20pF; ECX-32
kibuzzard-632DCC16: G***; kibuzzard-632DCC16

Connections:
+3V3: C8.1, C9.1, C10.1, C11.1, C15.1, R3.2, R5.2, R12.1, R14.1, U1.1 (VCCA), U2.1 (DEBUGGER), U2.7 (VCCIO), U2.25 (VOUT3V3)
+5V: C1.1, C2.1, C13.1, C14.1, F1.1, J20.3, R1.1, R47.1, R401.1, U2.26 (VCCIN), U2.30 (VBUS-DET)
+12V: C4.1, C5.1, C6.1, C12.1, C29.1, D501.1 (K), F2.2, J3.2, J4.2, J14.42, J20.1, R7.1, R8.1, R18.1, R25.1, R27.1
/ADC Circuitry/ADC1: J14.35, U6.8 (VIN0)
/ADC Circuitry/ADC2: J14.36, U6.13 (VIN1)
/ADC Circuitry/ADC3: J14.37, J17.1, R34.1
/ADC Circuitry/ADC4: J14.38, J18.1, R36.1
/ADC Circuitry/ADC5: J14.39, J16.1, R32.1
/ADC Circuitry/ADC6: J14.40, J19.1, R38.1
/ADC Circuitry/ADC7: R8.2, R9.1, U8.1 (A4)
/ADC Circuitry/ADC-CA0: J11.2, U6.1 (AS0)
/ADC Circuitry/ADC-CA1: J12.2, U6.16 (AS1)
/ADC Circuitry/ADCIN: C24.1, R30.1, TP9.1, U6.14 (ADCIN)
/ADC Circuitry/ADC_MUX: TP11.1, U6.9 (VIN2), U8.3 (A)
/ADC Circuitry/ADC_SELF_TEST: R23.1, U6.12 (VIN3)
/ADC Circuitry/Analog-MUX1: J17.2, U8.13 (A0)
/ADC Circuitry/Analog-MUX2: J18.2, U8.14 (A1)
/ADC Circuitry/Analog-MUX3: J16.2, U8.15 (A2)
/ADC Circuitry/Analog-MUX4: J19.2, U8.12 (A3)
/ADC Circuitry/Analog-MUX6: R1.2, R2.2, U8.5 (A5)
/ADC Circuitry/Analog-MUX8: R28.2, R29.1, TP10.1, U8.4 (A7)
/Connectors/CAN_AWAY+: J3.4, J15.2
/Connectors/CAN_AWAY-: J3.5, J13.2
/Connectors/CAN_N: J4.5, J6.1, J13.1, J14.44, J21.2, TP3.1
/Connectors/CAN_P: J4.4, J14.43, J15.1, J21.1, R16.1, TP2.1
/Connectors/DAC1: J14.27, U4.2 (VOUT0)
/Connectors/DAC2: J14.28, U4.1 (VOUT1)
/Connectors/DAC3: J14.29, U4.20 (VOUT2)
/Connectors/DAC4: J14.30, U4.19 (VOUT3)
/Connectors/DAC5: J14.31, U4.12 (VOUT4)
/Connectors/DAC6: J14.32, U4.11 (VOUT5)
/Connectors/DAC7: J14.33, U4.10 (VOUT6)
/Connectors/DAC8: J14.34, R23.2, U4.9 (VOUT7)
/Connectors/GPIO4: J14.12, U5.32 (P4)
/Connectors/GPIO5: J14.14, U5.30 (P5)
/Connectors/GPIO6: J14.16, U5.28 (P6)
/Connectors/GPIO7: J14.18, U5.26 (P7)
/Connectors/GPIO8: Q3.1 (G), R24.1, U5.5 (P8)
/Connectors/GPIO9: J14.04, U5.7 (P9)
/Connectors/GPIO10: J14.06, U5.9 (P10)
/Connectors/GPIO11: J14.08, U5.11
/Connectors/GPIO12: Q4.1 (G), R26.1, U5.6 (P12)
/Connectors/GPIO13: J14.03, U5.8 (P13)
/Connectors/GPIO14: J14.05, U5.10 (P14)
/Connectors/GPIO15: J14.07, U5.12 (P15)
/Connectors/GPIO16: J14.10, U5.13 (P16)
/Connectors/GPIO17: J14.09, U5.14 (P17)
/Connectors/GPIO18: R31.2, U5.15 (P18)
/Connectors/GPIO19: R31.1, U5.16 (P19), U8.11 (S0)
/Connectors/GPIO20: U5.17 (P20), U8.10 (S1)
/Connectors/GPIO21: U5.18 (P21), U8.9 (S2)
/Connectors/GPIO22: J14.23, U5.19 (P22)
/Connectors/GPIO23: J14.24, U5.20 (P23)
/Connectors/GPIO24: J14.21, U5.21 (P24)
/Connectors/GPIO25: J14.22, U5.22 (P25)
/Connectors/GPIO26: J14.19, U5.23 (P26)
/Connectors/GPIO27: J14.20, U5.24 (P27)
/Connectors/GPIO28: J14.17, U5.25 (P28)
/Connectors/GPIO29: J14.15, U5.27 (P29)
/Connectors/GPIO30: J14.13, U5.29 (P30)
/Connectors/GPIO31: J14.11, U5.31
/Connectors/SCL: J3.8, J4.8, R21.2, TP7.1, U1.7 (SCLB), U4.5 (SCL), U5.34 (SCL), U6.18 (SCL)
/Connectors/SDA: J3.7, J4.7, R22.2, TP6.1, U1.6 (SDAB), U4.16 (SDA), U5.33 (SDA), U6.17 (SDA)
/DAC/DAC-A0: J9.2, U4.6 (A0)
/DAC/DAC-A1: J10.2, U4.7 (A1)
/DAC/DAC-LDAC: Q1.1 (G), R13.1, U2.15 (GPIO2/SS3O/SUSP-OUT)
/GPIO/GPIO-AD0: J7.2, U5.4 (AD0)
/GPIO/GPIO-AD1: J8.2, U5.35 (AD1)
/USB->I2C/D+: J1.3 (D+), U2.23 (DP)
/USB->I2C/D-: J1.2 (D-), U2.22 (DM)
/USB->I2C/FT-VPP: SW1.1 (A), U2.29 (VPP)
/USB->I2C/SCL: R14.2, TP5.1, U1.3 (SDAA), U2.14 (GPIO1/SS2O/SDA)
/USB->I2C/SDA: R12.2, TP4.1, U1.2 (SCLA), U2.13 (GPIO0/SS1O/SCL)
/VBus Power/Lin-IN: C26.1, J20.2, U9.1 (IN), U9.2 (IN), U9.3 (IN), U9.4 (EN/UV), U9.7 (PGFB)
GND: C1.2, C2.2, C3.2, C4.2, C5.2, C6.2, C7.2, C8.2, C9.2, C10.2, C11.2, C12.2, C13.2, C14.2, C15.2, C16.2, C17.2, C18.2, C19.2, C20.2, C21.2, C22.2, C23.1, C24.2, C25.2, C26.2, C27.2, C28.2, C29.2, D1.1 (K), D3.1 (K), D7.2 (A), D8.1 (K), D501.2 (A), J1.4 (ID), J1.5 (GND), J1.6 (SHIELD), J1.7 (SHIELD), J1.8 (SHIELD), J1.9 (SHIELD), J1.10 (SHIELD), J1.11 (SHIELD), J2.2 (Shell), J3.1, J3.3, J3.6, J4.1, J4.3, J4.6, J7.3, J8.3, J9.3, J10.3, J11.3, J12.3, J14.01, J14.02, J14.25, J14.26, J14.41, J21.3, Q1.2 (S), Q2.2 (S), Q3.2 (S), Q4.2 (S), R2.1, R6.2, R9.2, R10.2, R11.1, R13.2, R15.2, R20.2, R24.2, R26.2, R33.2, R35.2, R37.2, R39.2, R40.2, R41.2, TP1.1, TP8.1, U1.4 (GND), U2.6 (DGND), U2.20 (UGND), U2.24 (UGND), U2.27 (AGND), U2.28 (DGND), U2.33 (GND), U4.8 (GAIN), U4.13 (GND), U4.14 (RSTSL), U5.2 (GND), U5.3 (GND), U6.6 (GND), U6.15 (GND), U7.2 (V-), U8.6 (~E), U8.7 (VEE), U8.8 (GND), U9.6 (ILIM), U9.9 (GND), U9.13 (GND), Y1.2, Y1.4
unnamed: C3.1, R4.2, U2.19 (XSCO), Y1.1
unnamed: C7.1, R4.1, U2.18 (XSCI), Y1.3
unnamed: C16.1, R19.2, U1.5 (EN), U1.8 (VCCB)
unnamed: C17.1, JP3.1 (A), U4.3 (VDD), U4.4 (VLOGIC), U4.18 (VREF)
unnamed: C18.1, C19.1, JP2.1 (A), U5.36 (V+)
unnamed: C20.1, C21.1, JP1.1 (A), U6.2 (*RESET), U6.3 (VDD), U6.5 (REFIN/REFOUT), U6.20 (VDRIVE)
unnamed: C22.1, U6.4 (REGCAP)
unnamed: C27.1, R42.1, R43.2, U9.10 (OUTS), U9.11 (OUT), U9.12 (OUT)
unnamed: C28.1, R40.1, R41.1, U9.8 (SET)
unnamed: D1.2 (A), R47.2
unnamed: D3.2 (A), R7.2
unnamed: D4.1 (K), Q2.3 (D)
unnamed: D4.2 (A), R18.2
unnamed: D5.1 (K), Q3.3 (D)
unnamed: D5.2 (A), R25.2
unnamed: D6.1 (K), Q4.3 (D)
unnamed: D6.2 (A), R27.2
unnamed: D7.1 (K), R29.2
unnamed: D8.2 (A), R42.2
unnamed: F1.2, J1.1 (VCC)
unnamed: F2.1, J2.1 (center)
unnamed: J6.2, R16.2
unnamed: J16.3, R32.2, R33.1
unnamed: J17.3, R34.2, R35.1
unnamed: J18.3, R36.2, R37.1
unnamed: J19.3, R38.2, R39.1
unnamed: Q1.3 (D), R17.2, U4.15 (LDAC_n)
unnamed: Q2.1 (G), R15.1, U2.16 (GPIO3/WAKEUP/INTR)
unnamed: R3.1, U2.2 (STEST_RESET_n)
unnamed: R5.1, U2.3 (RESET_n)
unnamed: R6.1, U2.21 (RREF)
unnamed: R10.1, U2.4 (DCNF0)
unnamed: R11.2, U2.5 (DCNF1)
unnamed: R20.1, U5.1 (ISET)
unnamed: R30.2, U7.1, U7.4 (-)
unnamed: R401.2, SW1.3 (B)
unnamed: U6.7 (MUXOUT), U7.3 (+)
VBUS: C23.2, C25.1, J7.1, J8.1, J9.1, J10.1, J11.1, J12.1, JP1.2 (B), JP2.2 (B), JP3.2 (B), R17.1, R19.1, R21.1, R22.1, R28.1, R43.1, TP12.1, U4.17 (RESET_n), U7.5 (V+), U8.16 (VCC)

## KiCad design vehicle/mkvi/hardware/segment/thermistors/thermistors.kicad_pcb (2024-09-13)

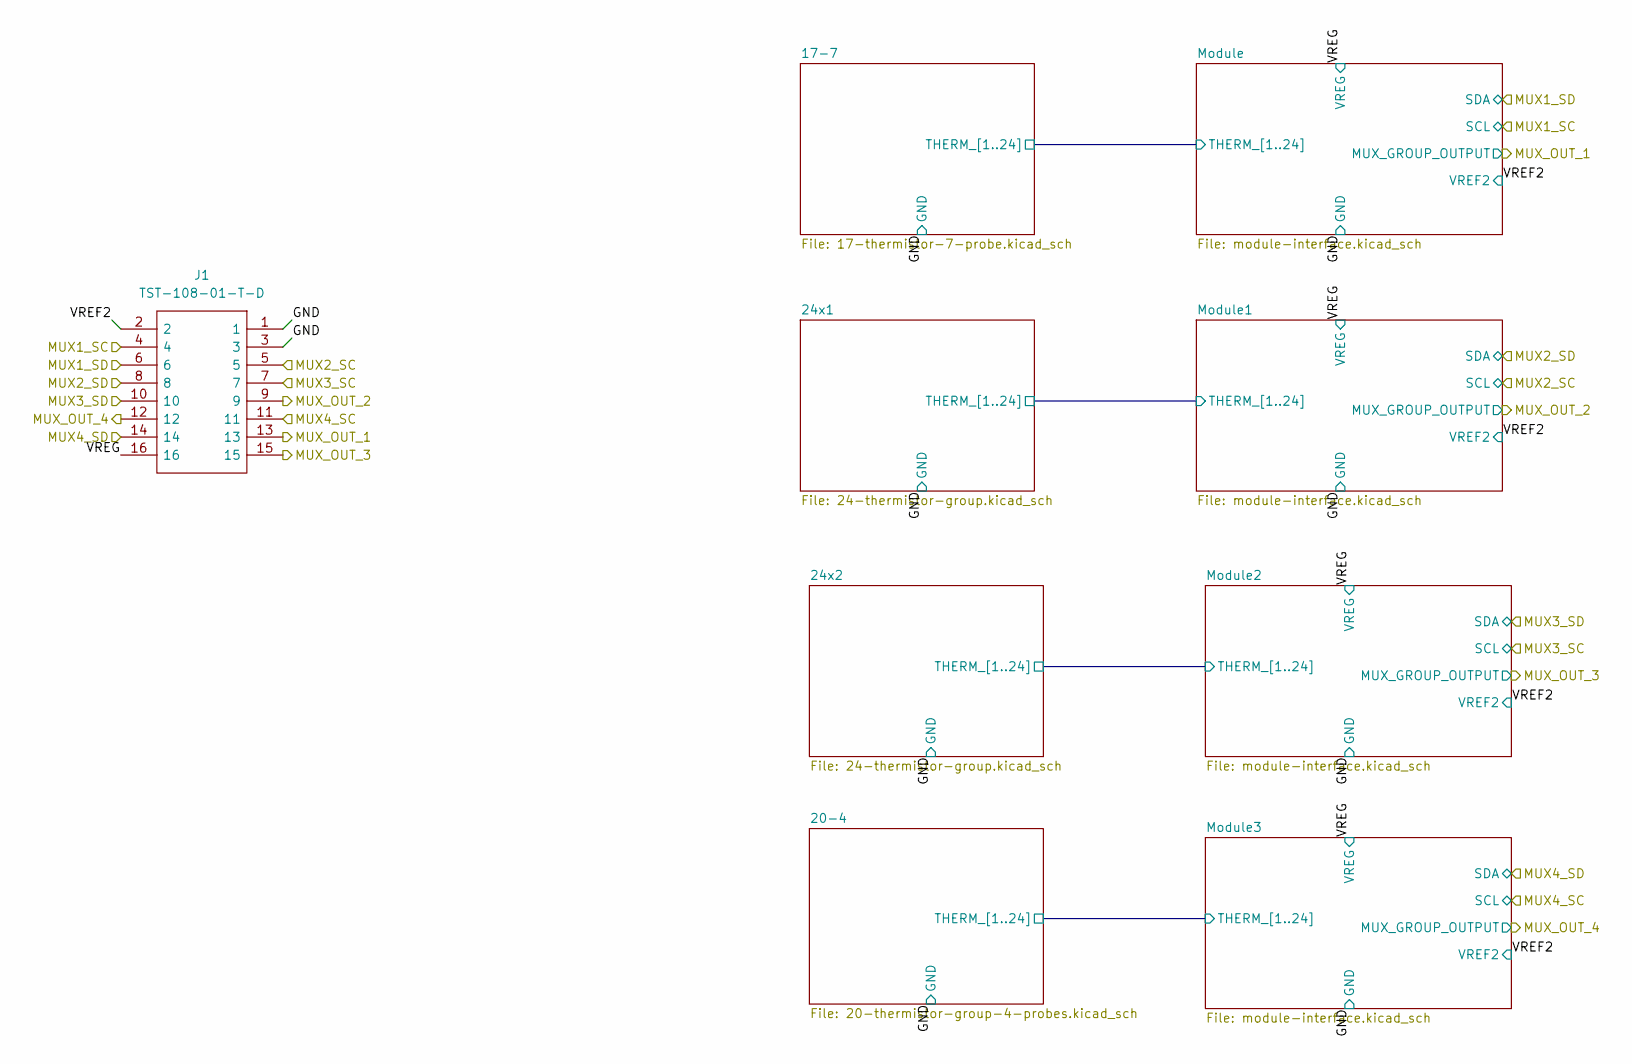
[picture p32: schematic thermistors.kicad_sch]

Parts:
J1: TST-108-01-T-D; TST-108-XX-T-D; MPN TST-108-01-T-D

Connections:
/GND: J1.1, J1.3; also elsewhere on the board
/MUX1_SC: J1.4; also elsewhere on the board
/MUX1_SD: J1.6; also elsewhere on the board
/MUX2_SC: J1.5; also elsewhere on the board
/MUX2_SD: J1.8; also elsewhere on the board
/MUX3_SC: J1.7; also elsewhere on the board
/MUX3_SD: J1.10; also elsewhere on the board
/MUX4_SC: J1.11; also elsewhere on the board
/MUX4_SD: J1.14; also elsewhere on the board
/MUX_OUT_1: J1.13; also elsewhere on the board
/MUX_OUT_2: J1.9; also elsewhere on the board
/MUX_OUT_3: J1.15; also elsewhere on the board
/MUX_OUT_4: J1.12; also elsewhere on the board
/VREF2: J1.2; also elsewhere on the board
/VREG: J1.16; also elsewhere on the board

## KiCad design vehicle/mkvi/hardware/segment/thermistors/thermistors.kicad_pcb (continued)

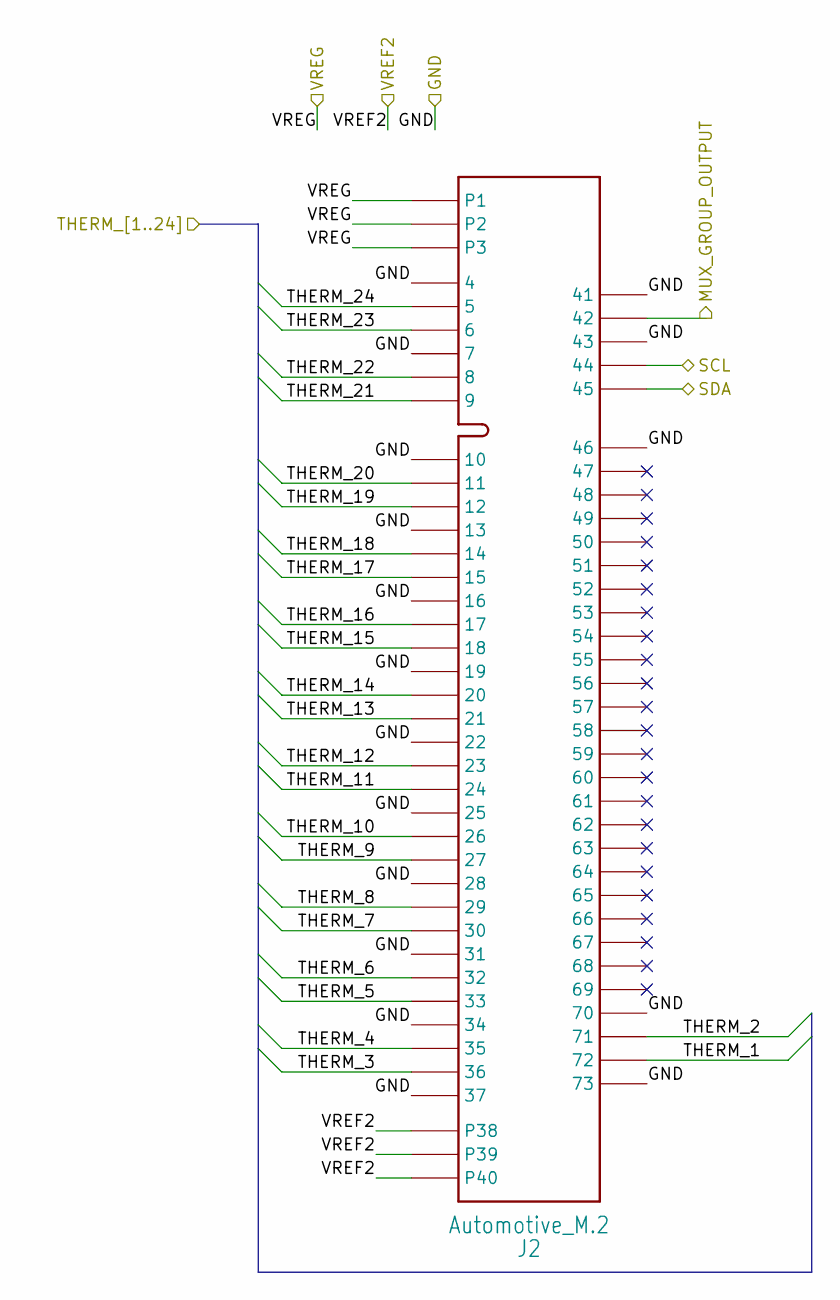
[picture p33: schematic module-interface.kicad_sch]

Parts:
J2: Automotive_M.2; MKVI_DA_Module; MPN CNU027S-067-2001-VE

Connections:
/17-7/THERM_1: J2.72; also elsewhere on the board
/17-7/THERM_2: J2.71; also elsewhere on the board
/17-7/THERM_3: J2.36; also elsewhere on the board
/17-7/THERM_4: J2.35; also elsewhere on the board
/17-7/THERM_5: J2.33; also elsewhere on the board
/17-7/THERM_6: J2.32; also elsewhere on the board
/17-7/THERM_7: J2.30; also elsewhere on the board
/17-7/THERM_8: J2.29; also elsewhere on the board
/17-7/THERM_9: J2.27; also elsewhere on the board
/17-7/THERM_10: J2.26; also elsewhere on the board
/17-7/THERM_11: J2.24; also elsewhere on the board
/17-7/THERM_12: J2.23; also elsewhere on the board
/17-7/THERM_13: J2.21; also elsewhere on the board
/17-7/THERM_14: J2.20; also elsewhere on the board
/17-7/THERM_15: J2.18; also elsewhere on the board
/17-7/THERM_16: J2.17; also elsewhere on the board
/17-7/THERM_17: J2.15; also elsewhere on the board
/17-7/THERM_18: J2.14; also elsewhere on the board
/17-7/THERM_19: J2.12; also elsewhere on the board
/17-7/THERM_20: J2.11; also elsewhere on the board
/17-7/THERM_21: J2.9; also elsewhere on the board
/17-7/THERM_22: J2.8; also elsewhere on the board
/17-7/THERM_23: J2.6; also elsewhere on the board
/17-7/THERM_24: J2.5; also elsewhere on the board
/GND: J2.4, J2.7, J2.10, J2.13, J2.16, J2.19, J2.22, J2.25, J2.28, J2.31, J2.34, J2.37, J2.41, J2.43, J2.46, J2.70, J2.73; also elsewhere on the board
/MUX1_SC: J2.44; also elsewhere on the board
/MUX1_SD: J2.45; also elsewhere on the board
/MUX_OUT_1: J2.42; also elsewhere on the board
/VREF2: J2.P38, J2.P39, J2.P40; also elsewhere on the board
/VREG: J2.P1, J2.P2, J2.P3; also elsewhere on the board

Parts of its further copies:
J3, J4, J5: Automotive_M.2; MKVI_DA_Module; MPN CNU027S-067-2001-VE

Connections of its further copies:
/20-4/THERM_1: J5.72; also elsewhere on the board
/20-4/THERM_2: J5.71; also elsewhere on the board
/20-4/THERM_3: J5.36; also elsewhere on the board
/20-4/THERM_4: J5.35; also elsewhere on the board
/20-4/THERM_5: J5.33; also elsewhere on the board
/20-4/THERM_6: J5.32; also elsewhere on the board
/20-4/THERM_7: J5.30; also elsewhere on the board
/20-4/THERM_8: J5.29; also elsewhere on the board
/20-4/THERM_9: J5.27; also elsewhere on the board
/20-4/THERM_10: J5.26; also elsewhere on the board
/20-4/THERM_11: J5.24; also elsewhere on the board
/20-4/THERM_12: J5.23; also elsewhere on the board
/20-4/THERM_13: J5.21; also elsewhere on the board
/20-4/THERM_14: J5.20; also elsewhere on the board
/20-4/THERM_15: J5.18; also elsewhere on the board
/20-4/THERM_16: J5.17; also elsewhere on the board
/20-4/THERM_17: J5.15; also elsewhere on the board
/20-4/THERM_18: J5.14; also elsewhere on the board
/20-4/THERM_19: J5.12; also elsewhere on the board
/20-4/THERM_20: J5.11; also elsewhere on the board
/20-4/THERM_21: J5.9; also elsewhere on the board
/20-4/THERM_22: J5.8; also elsewhere on the board
/20-4/THERM_23: J5.6; also elsewhere on the board
/20-4/THERM_24: J5.5; also elsewhere on the board
/24x1/THERM_1: J3.72; also elsewhere on the board
/24x1/THERM_2: J3.71; also elsewhere on the board
/24x1/THERM_3: J3.36; also elsewhere on the board
/24x1/THERM_4: J3.35; also elsewhere on the board
/24x1/THERM_5: J3.33; also elsewhere on the board
/24x1/THERM_6: J3.32; also elsewhere on the board
/24x1/THERM_7: J3.30; also elsewhere on the board
/24x1/THERM_8: J3.29; also elsewhere on the board
/24x1/THERM_9: J3.27; also elsewhere on the board
/24x1/THERM_10: J3.26; also elsewhere on the board
/24x1/THERM_11: J3.24; also elsewhere on the board
/24x1/THERM_12: J3.23; also elsewhere on the board
/24x1/THERM_13: J3.21; also elsewhere on the board
/24x1/THERM_14: J3.20; also elsewhere on the board
/24x1/THERM_15: J3.18; also elsewhere on the board
/24x1/THERM_16: J3.17; also elsewhere on the board
/24x1/THERM_17: J3.15; also elsewhere on the board
/24x1/THERM_18: J3.14; also elsewhere on the board
/24x1/THERM_19: J3.12; also elsewhere on the board
/24x1/THERM_20: J3.11; also elsewhere on the board
/24x1/THERM_21: J3.9; also elsewhere on the board
/24x1/THERM_22: J3.8; also elsewhere on the board
/24x1/THERM_23: J3.6; also elsewhere on the board
/24x1/THERM_24: J3.5; also elsewhere on the board
/24x2/THERM_1: J4.72; also elsewhere on the board
/24x2/THERM_2: J4.71; also elsewhere on the board
/24x2/THERM_3: J4.36; also elsewhere on the board
/24x2/THERM_4: J4.35; also elsewhere on the board
/24x2/THERM_5: J4.33; also elsewhere on the board
/24x2/THERM_6: J4.32; also elsewhere on the board
/24x2/THERM_7: J4.30; also elsewhere on the board
/24x2/THERM_8: J4.29; also elsewhere on the board
/24x2/THERM_9: J4.27; also elsewhere on the board
/24x2/THERM_10: J4.26; also elsewhere on the board
/24x2/THERM_11: J4.24; also elsewhere on the board
/24x2/THERM_12: J4.23; also elsewhere on the board
/24x2/THERM_13: J4.21; also elsewhere on the board
/24x2/THERM_14: J4.20; also elsewhere on the board
/24x2/THERM_15: J4.18; also elsewhere on the board
/24x2/THERM_16: J4.17; also elsewhere on the board
/24x2/THERM_17: J4.15; also elsewhere on the board
/24x2/THERM_18: J4.14; also elsewhere on the board
/24x2/THERM_19: J4.12; also elsewhere on the board
/24x2/THERM_20: J4.11; also elsewhere on the board
/24x2/THERM_21: J4.9; also elsewhere on the board
/24x2/THERM_22: J4.8; also elsewhere on the board
/24x2/THERM_23: J4.6; also elsewhere on the board
/24x2/THERM_24: J4.5; also elsewhere on the board
/GND: J3.4, J3.7, J3.10, J3.13, J3.16, J3.19, J3.22, J3.25, J3.28, J3.31, J3.34, J3.37, J3.41, J3.43, J3.46, J3.70, J3.73, J4.4, J4.7, J4.10, J4.13, J4.16, J4.19, J4.22, J4.25, J4.28, J4.31, J4.34, J4.37, J4.41, J4.43, J4.46, J4.70, J4.73, J5.4, J5.7, J5.10, J5.13, J5.16, J5.19, J5.22, J5.25, J5.28, J5.31, J5.34, J5.37, J5.41, J5.43, J5.46, J5.70, J5.73; also elsewhere on the board
/MUX2_SC: J3.44; also elsewhere on the board
/MUX2_SD: J3.45; also elsewhere on the board
/MUX3_SC: J4.44; also elsewhere on the board
/MUX3_SD: J4.45; also elsewhere on the board
/MUX4_SC: J5.44; also elsewhere on the board
/MUX4_SD: J5.45; also elsewhere on the board
/MUX_OUT_2: J3.42; also elsewhere on the board
/MUX_OUT_3: J4.42; also elsewhere on the board
/MUX_OUT_4: J5.42; also elsewhere on the board
/VREF2: J3.P38, J3.P39, J3.P40, J4.P38, J4.P39, J4.P40, J5.P38, J5.P39, J5.P40; also elsewhere on the board
/VREG: J3.P1, J3.P2, J3.P3, J4.P1, J4.P2, J4.P3, J5.P1, J5.P2, J5.P3; also elsewhere on the board

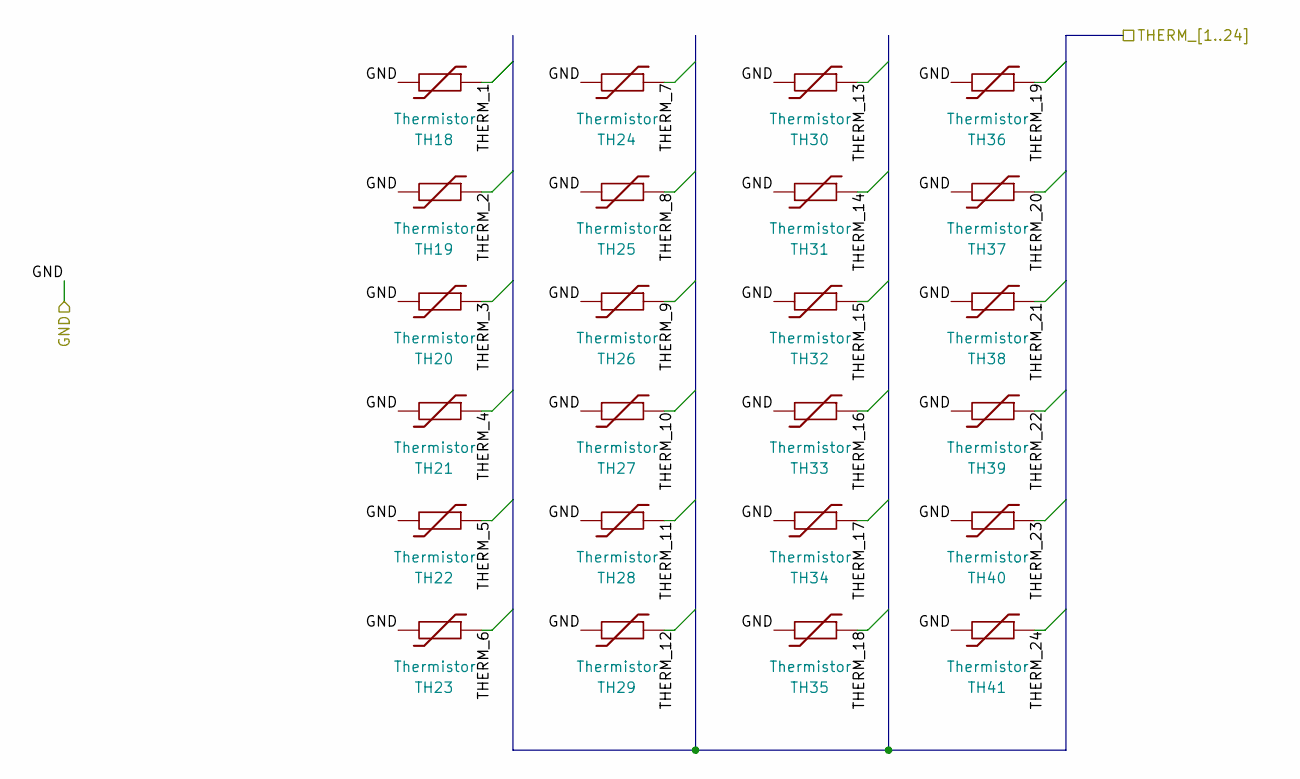
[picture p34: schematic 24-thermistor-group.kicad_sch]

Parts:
TH18, TH19, TH20, TH21, TH22, TH23, TH24, TH25, TH26, TH27, TH28, TH29, TH30, TH31, TH32, TH33, TH34, TH35, TH36, TH37, TH38, TH39, TH40, TH41: Thermistor; R_0603; MPN 273-TX06F104F4100ERDKR-ND

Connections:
/24x1/THERM_1: TH18.1; also elsewhere on the board
/24x1/THERM_2: TH19.1; also elsewhere on the board
/24x1/THERM_3: TH20.1; also elsewhere on the board
/24x1/THERM_4: TH21.1; also elsewhere on the board
/24x1/THERM_5: TH22.1; also elsewhere on the board
/24x1/THERM_6: TH23.1; also elsewhere on the board
/24x1/THERM_7: TH24.1; also elsewhere on the board
/24x1/THERM_8: TH25.1; also elsewhere on the board
/24x1/THERM_9: TH26.1; also elsewhere on the board
/24x1/THERM_10: TH27.1; also elsewhere on the board
/24x1/THERM_11: TH28.1; also elsewhere on the board
/24x1/THERM_12: TH29.1; also elsewhere on the board
/24x1/THERM_13: TH30.1; also elsewhere on the board
/24x1/THERM_14: TH31.1; also elsewhere on the board
/24x1/THERM_15: TH32.1; also elsewhere on the board
/24x1/THERM_16: TH33.1; also elsewhere on the board
/24x1/THERM_17: TH34.1; also elsewhere on the board
/24x1/THERM_18: TH35.1; also elsewhere on the board
/24x1/THERM_19: TH36.1; also elsewhere on the board
/24x1/THERM_20: TH37.1; also elsewhere on the board
/24x1/THERM_21: TH38.1; also elsewhere on the board
/24x1/THERM_22: TH39.1; also elsewhere on the board
/24x1/THERM_23: TH40.1; also elsewhere on the board
/24x1/THERM_24: TH41.1; also elsewhere on the board
/GND: TH18.2, TH19.2, TH20.2, TH21.2, TH22.2, TH23.2, TH24.2, TH25.2, TH26.2, TH27.2, TH28.2, TH29.2, TH30.2, TH31.2, TH32.2, TH33.2, TH34.2, TH35.2, TH36.2, TH37.2, TH38.2, TH39.2, TH40.2, TH41.2; also elsewhere on the board

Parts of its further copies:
TH42, TH43, TH44, TH45, TH46, TH47, TH48, TH49, TH50, TH51, TH52, TH53, TH54, TH55, TH56, TH57, TH58, TH59, TH60, TH61, TH62, TH63, TH64, TH65: Thermistor; R_0603; MPN 273-TX06F104F4100ERDKR-ND

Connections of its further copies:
/24x2/THERM_1: TH42.1; also elsewhere on the board
/24x2/THERM_2: TH43.1; also elsewhere on the board
/24x2/THERM_3: TH44.1; also elsewhere on the board
/24x2/THERM_4: TH45.1; also elsewhere on the board
/24x2/THERM_5: TH46.1; also elsewhere on the board
/24x2/THERM_6: TH47.1; also elsewhere on the board
/24x2/THERM_7: TH48.1; also elsewhere on the board
/24x2/THERM_8: TH49.1; also elsewhere on the board
/24x2/THERM_9: TH50.1; also elsewhere on the board
/24x2/THERM_10: TH51.1; also elsewhere on the board
/24x2/THERM_11: TH52.1; also elsewhere on the board
/24x2/THERM_12: TH53.1; also elsewhere on the board
/24x2/THERM_13: TH54.1; also elsewhere on the board
/24x2/THERM_14: TH55.1; also elsewhere on the board
/24x2/THERM_15: TH56.1; also elsewhere on the board
/24x2/THERM_16: TH57.1; also elsewhere on the board
/24x2/THERM_17: TH58.1; also elsewhere on the board
/24x2/THERM_18: TH59.1; also elsewhere on the board
/24x2/THERM_19: TH60.1; also elsewhere on the board
/24x2/THERM_20: TH61.1; also elsewhere on the board
/24x2/THERM_21: TH62.1; also elsewhere on the board
/24x2/THERM_22: TH63.1; also elsewhere on the board
/24x2/THERM_23: TH64.1; also elsewhere on the board
/24x2/THERM_24: TH65.1; also elsewhere on the board
/GND: TH42.2, TH43.2, TH44.2, TH45.2, TH46.2, TH47.2, TH48.2, TH49.2, TH50.2, TH51.2, TH52.2, TH53.2, TH54.2, TH55.2, TH56.2, TH57.2, TH58.2, TH59.2, TH60.2, TH61.2, TH62.2, TH63.2, TH64.2, TH65.2; also elsewhere on the board


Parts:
J6, J7, J8, J9, J10, J11, J12: MicroFit_RA_2; MPN 0436500201
TH1, TH2, TH3, TH4, TH5, TH6, TH7, TH8, TH9, TH10, TH11, TH12, TH13, TH14, TH15, TH16, TH17: Thermistor; R_0603; MPN 273-TX06F104F4100ERDKR-ND

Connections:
/17-7/THERM_1: J6.1; also elsewhere on the board
/17-7/THERM_2: J7.1; also elsewhere on the board
/17-7/THERM_3: J8.1; also elsewhere on the board
/17-7/THERM_4: J9.1; also elsewhere on the board
/17-7/THERM_5: J10.1; also elsewhere on the board
/17-7/THERM_6: J11.1; also elsewhere on the board
/17-7/THERM_7: J12.1; also elsewhere on the board
/17-7/THERM_8: TH1.1; also elsewhere on the board
/17-7/THERM_9: TH2.1; also elsewhere on the board
/17-7/THERM_10: TH3.1; also elsewhere on the board
/17-7/THERM_11: TH4.1; also elsewhere on the board
/17-7/THERM_12: TH5.1; also elsewhere on the board
/17-7/THERM_13: TH6.1; also elsewhere on the board
/17-7/THERM_14: TH7.1; also elsewhere on the board
/17-7/THERM_15: TH8.1; also elsewhere on the board
/17-7/THERM_16: TH9.1; also elsewhere on the board
/17-7/THERM_17: TH10.1; also elsewhere on the board
/17-7/THERM_18: TH11.1; also elsewhere on the board
/17-7/THERM_19: TH12.1; also elsewhere on the board
/17-7/THERM_20: TH13.1; also elsewhere on the board
/17-7/THERM_21: TH14.1; also elsewhere on the board
/17-7/THERM_22: TH15.1; also elsewhere on the board
/17-7/THERM_23: TH16.1; also elsewhere on the board
/17-7/THERM_24: TH17.1; also elsewhere on the board
/GND: J6.2, J7.2, J8.2, J9.2, J10.2, J11.2, J12.2, TH1.2, TH2.2, TH3.2, TH4.2, TH5.2, TH6.2, TH7.2, TH8.2, TH9.2, TH10.2, TH11.2, TH12.2, TH13.2, TH14.2, TH15.2, TH16.2, TH17.2; also elsewhere on the board


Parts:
J13, J14, J15, J16: MicroFit_RA_2; MPN 0436500201
TH66, TH67, TH68, TH69, TH70, TH71, TH72, TH73, TH74, TH75, TH76, TH77, TH78, TH79, TH80, TH81, TH82, TH83, TH84, TH85: Thermistor; R_0603; MPN 273-TX06F104F4100ERDKR-ND

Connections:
/20-4/THERM_1: J13.1; also elsewhere on the board
/20-4/THERM_2: J14.1; also elsewhere on the board
/20-4/THERM_3: J15.1; also elsewhere on the board
/20-4/THERM_4: J16.1; also elsewhere on the board
/20-4/THERM_5: TH66.1; also elsewhere on the board
/20-4/THERM_6: TH67.1; also elsewhere on the board
/20-4/THERM_7: TH68.1; also elsewhere on the board
/20-4/THERM_8: TH69.1; also elsewhere on the board
/20-4/THERM_9: TH70.1; also elsewhere on the board
/20-4/THERM_10: TH71.1; also elsewhere on the board
/20-4/THERM_11: TH72.1; also elsewhere on the board
/20-4/THERM_12: TH73.1; also elsewhere on the board
/20-4/THERM_13: TH74.1; also elsewhere on the board
/20-4/THERM_14: TH75.1; also elsewhere on the board
/20-4/THERM_15: TH76.1; also elsewhere on the board
/20-4/THERM_16: TH77.1; also elsewhere on the board
/20-4/THERM_17: TH78.1; also elsewhere on the board
/20-4/THERM_18: TH79.1; also elsewhere on the board
/20-4/THERM_19: TH80.1; also elsewhere on the board
/20-4/THERM_20: TH81.1; also elsewhere on the board
/20-4/THERM_21: TH82.1; also elsewhere on the board
/20-4/THERM_22: TH83.1; also elsewhere on the board
/20-4/THERM_23: TH84.1; also elsewhere on the board
/20-4/THERM_24: TH85.1; also elsewhere on the board
/GND: J13.2, J14.2, J15.2, J16.2, TH66.2, TH67.2, TH68.2, TH69.2, TH70.2, TH71.2, TH72.2, TH73.2, TH74.2, TH75.2, TH76.2, TH77.2, TH78.2, TH79.2, TH80.2, TH81.2, TH82.2, TH83.2, TH84.2, TH85.2; also elsewhere on the board



Board: 2 copper layers, 431.8 x 175.0 mm, 105 parts (101 on the bottom side), 111 nets.

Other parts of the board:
QR*****: hw.oem.to/6_THERMAL_1; QR_6_THERMAL_1
kibuzzard-63B8B2B4: G***; kibuzzard-63B8B2B4
kibuzzard-63B8B2E9: G***; kibuzzard-63B8B2E9
kibuzzard-63BC82F4: G***; kibuzzard-63BC82F4

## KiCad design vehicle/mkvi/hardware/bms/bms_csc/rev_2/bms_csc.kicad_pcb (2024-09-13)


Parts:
C1, C2, C3: C_1uF; C_0603; MPN CL10B105KA8NNNC
C4: C_0.1uF; C_0603; MPN CL10B104KB8NNWC
Q1: NSS1C201MZ4; SOT-223; MPN NSS1C201MZ4
R1, R2: R_1K; R_0603; MPN RMCF0603FT1K00
R3: R_100; R_0603; MPN RMCF0603FT100R
TP9, TP10, TP11, TP12, TP13, TP14, TP15, TP16, TP17, TP18: TP_1mm; TestPoint_Pad_D1.0mm
TP19, TP20: TP_SMD; Test_Point_SMD; MPN 5019
U1: ADBMS1818; LQFP-64-1EP_12x12_P0.5; MPN ADBMS1818
U2: MCP6001T-I-LT; SOT-353_SC-70-5; MPN MCP6001T-I/OT

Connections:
/C1: U1.36 (C1); also elsewhere on the board
/C2: U1.34 (C2); also elsewhere on the board
/C3: U1.32 (C3); also elsewhere on the board
/C4: U1.30 (C4); also elsewhere on the board
/C5: U1.28 (C5); also elsewhere on the board
/C6: U1.26 (C6); also elsewhere on the board
/C7: U1.24 (C7); also elsewhere on the board
/C8: U1.22 (C8); also elsewhere on the board
/C9: U1.20 (C9); also elsewhere on the board
/C10: U1.18 (C10); also elsewhere on the board
/C11: U1.16 (C11); also elsewhere on the board
/C12: U1.14 (C12); also elsewhere on the board
/C13: U1.12 (C13); also elsewhere on the board
/C14: U1.10 (C14); also elsewhere on the board
/C15: U1.8 (C15); also elsewhere on the board
/C16: U1.6 (C16); also elsewhere on the board
/C17: U1.4 (C17); also elsewhere on the board
/C18: U1.2 (C18); also elsewhere on the board
/IMA: U1.61 (CSBIMA); also elsewhere on the board
/IMB: U1.63 (IMB); also elsewhere on the board
/IPA: U1.62 (SCKIPA); also elsewhere on the board
/IPB: U1.64 (IPB); also elsewhere on the board
/MUX1_SC: TP12.1; also elsewhere on the board
/MUX1_SD: TP11.1; also elsewhere on the board
/MUX2_SC: TP14.1; also elsewhere on the board
/MUX2_SD: TP13.1; also elsewhere on the board
/MUX3_SC: TP16.1; also elsewhere on the board
/MUX3_SD: TP15.1; also elsewhere on the board
/MUX4_SC: TP18.1; also elsewhere on the board
/MUX4_SD: TP17.1; also elsewhere on the board
/MUX_OUT_1: U1.39 (GPIO1); also elsewhere on the board
/MUX_OUT_2: U1.40 (GPIO2); also elsewhere on the board
/MUX_OUT_3: U1.41 (GPIO3); also elsewhere on the board
/MUX_OUT_4: U1.44 (GPIO6); also elsewhere on the board
/S1: U1.37 (S1); also elsewhere on the board
/S2: U1.35 (S2); also elsewhere on the board
/S3: U1.33 (S3); also elsewhere on the board
/S4: U1.31 (S4); also elsewhere on the board
/S5: U1.29 (S5); also elsewhere on the board
/S6: U1.27 (S6); also elsewhere on the board
/S7: U1.25 (S7); also elsewhere on the board
/S8: U1.23 (S8); also elsewhere on the board
/S9: U1.21 (S9); also elsewhere on the board
/S10: U1.19 (S10); also elsewhere on the board
/S11: U1.17 (S11); also elsewhere on the board
/S12: U1.15 (S12); also elsewhere on the board
/S13: U1.13 (S13); also elsewhere on the board
/S14: U1.11 (S14); also elsewhere on the board
/S15: U1.9 (S15); also elsewhere on the board
/S16: U1.7 (S16); also elsewhere on the board
/S17: U1.5 (S17); also elsewhere on the board
/S18: U1.3 (S18); also elsewhere on the board
/SCL: TP9.1, U1.43 (GPIO5); also elsewhere on the board
/SDA: TP10.1, U1.42 (GPIO4); also elsewhere on the board
/V+: R3.1, U1.1 (V+); also elsewhere on the board
/VDRIVE: Q1.1 (B), U1.49 (VDRIVE)
/VREF2: U2.1, U2.4 (-); also elsewhere on the board
/VREG: C3.2, Q1.3 (E), TP19.1, U1.48 (VREG), U1.55 (ISOMD), U2.5 (V+); also elsewhere on the board
unnamed: C4.1, Q1.2 (C), Q1.4 (C), R3.2
unnamed: R2.2, U1.57 (IBIAS)
unnamed: R1.2, R2.1, U1.58 (ICMP)
unnamed: C2.2, U1.51 (VREF1)
unnamed: C1.2, U1.50 (VREF2), U2.3 (+)

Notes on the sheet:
pg. 13 To use isoSPI
Hierarchical, click box to view subpage
From Power Board
Power as heat for the transistor (70V-5V)*35mA = 2.275W
pg. 68 of datasheet
Cells 1-18
ADBMS1818 Chip Pinout
Outputs of each DA module Group 1-4 of Muxes
RB2
2 isoSPI- A -> BMS Core 2 isoSPI+ B -> Next CSC
COMMUNICATION INTERFACES
Voltage Filtering and Balancing
Voltage Follower (Supply Current to Thermistors)
ADBMS1818 Chip Power
VREG VREF2 GND SCL SDA Output
VREG: Supply Voltage, ~5V VREF2: 2nd Reference Voltage, ~3V VDRIVE: Output voltage, ~5.7V
pg. 38 GPIO4 & GPIO5
Connections to DA Modules
To Voltage Filtering Hierarchical Sheet
ADBMS1818
Cell Connects
RB1
POWER FLAGS
M.2 CONNECTOR
GND is negative terminal, "Cell 0"
TEST POINTS


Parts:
C5, C6, C7, C8: C_10nF; C_0603; MPN CL10B103KB8NNNC
J1, J2: MicroFit_RA_2; MPN 0436500201
R4, R5, R6, R7: R_60.4; R_0603; MPN RMCF0603FT60R4
T1: HM2112ZNLT; MPN HM2112ZNLT
TP1, TP2, TP3, TP4, TP5, TP6, TP7, TP8: TP_SMD; Test_Point_SMD; MPN 5019

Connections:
/IMA: R4.1, T1.12, TP2.1; also elsewhere on the board
/IMB: R6.1, T1.9, TP3.1; also elsewhere on the board
/IPA: R5.2, T1.10, TP1.1; also elsewhere on the board
/IPB: R7.2, T1.7, TP4.1; also elsewhere on the board
unnamed: C5.1, R4.2, R5.1
unnamed: C6.1, R6.2, R7.1
unnamed: C7.1, T1.11
unnamed: C8.1, T1.8
unnamed: J1.1, T1.1, TP5.1
unnamed: J1.2, T1.3, TP6.1
unnamed: J2.1, T1.4, TP7.1
unnamed: J2.2, T1.6, TP8.1

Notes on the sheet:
isoSPI B up the daisy chain
TRANSFORMER
isoSPI Transformer
NEW PART - HM2112ZNLT
isoSPI A towards Core
Wire isoSPI on board, use twisted wires off board


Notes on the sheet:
BUS CONNECTIONS
C18 needs to be connected to the topmost cell of pack!
For getting voltage measurements from the ADBMS1818 chip
cont.
Cell Pins
Direct connection to Cell terminals on battery (thru Power Board on segment)
C Pins
V+ of segment
Filtering RC circuit as depicted on ADBMS1818 datasheet pg. 72
V- of segment
FILTER AND BALANCE CIRCUITS
S Pins
"Discharge pins" Purpose is to balance cells by discharging
Split into Hierarchical Sheet (Boxes) KiCAD duplicates for you, but each requires same connections

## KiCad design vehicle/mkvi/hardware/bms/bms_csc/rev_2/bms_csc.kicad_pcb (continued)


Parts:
H1: M.2_MountingHole; M.2_Mount
J3: Automotive_M.2_Edge_Connector; MPN N/A

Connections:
/CELL1: J3.56; also elsewhere on the board
/CELL2: J3.57; also elsewhere on the board
/CELL3: J3.58; also elsewhere on the board
/CELL4: J3.59; also elsewhere on the board
/CELL5: J3.60; also elsewhere on the board
/CELL6: J3.61; also elsewhere on the board
/CELL7: J3.62; also elsewhere on the board
/CELL8: J3.63; also elsewhere on the board
/CELL9: J3.64; also elsewhere on the board
/CELL10: J3.65; also elsewhere on the board
/CELL11: J3.66; also elsewhere on the board
/CELL12: J3.67; also elsewhere on the board
/CELL13: J3.68; also elsewhere on the board
/CELL14: J3.69; also elsewhere on the board
/CELL15: J3.70; also elsewhere on the board
/CELL16: J3.71; also elsewhere on the board
/CELL17: J3.72; also elsewhere on the board
/CELL18: J3.73; also elsewhere on the board
/MUX1_SC: J3.18; also elsewhere on the board
/MUX1_SD: J3.17; also elsewhere on the board
/MUX2_SC: J3.15; also elsewhere on the board
/MUX2_SD: J3.14; also elsewhere on the board
/MUX3_SC: J3.12; also elsewhere on the board
/MUX3_SD: J3.11; also elsewhere on the board
/MUX4_SC: J3.9; also elsewhere on the board
/MUX4_SD: J3.8; also elsewhere on the board
/MUX_OUT_1: J3.6; also elsewhere on the board
/MUX_OUT_2: J3.42; also elsewhere on the board
/MUX_OUT_3: J3.5; also elsewhere on the board
/MUX_OUT_4: J3.41; also elsewhere on the board
/V+: J3.36, J3.37; also elsewhere on the board
/VREF2: J3.P38, J3.P39, J3.P40; also elsewhere on the board
/VREG: J3.P1, J3.P2, J3.P3; also elsewhere on the board

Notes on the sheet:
This M.2 Connector allows this board to slot in directly to the segment's "Power Board", which has traces to all the cell terminals and connections out to the "Thermistor board", which has all the thermistor connections. The "Power Board" and "Thermistor board" are structural boards of the segments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
Connects to DA modules from Power board to Thermistor board
No Connect To follow isoSPI transformer rules
Communication to DA modules 1-4
Connects to cells terminals through the Power board
THERMISTORS - TEMPS
M.2 CONNECTOR
CELLS - VOLTAGES
Outputs of DA modules 1-4


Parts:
IC1: PCA9545APW; SOP65P640X110-20N; MPN PCA9545APW
R8, R9, R10, R11, R12, R13, R14: R_4.99K; R_0603; MPN RMCF0603FT4K99
U3: 24AA01; SOT-23-5_OEM_24AA01; MPN CAT24AA01TDI-GT3OSCT-ND

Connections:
/MUX1_SC: IC1.6 (SC0); also elsewhere on the board
/MUX1_SD: IC1.5 (SD0); also elsewhere on the board
/MUX2_SC: IC1.9 (SC1); also elsewhere on the board
/MUX2_SD: IC1.8 (SD1); also elsewhere on the board
/MUX3_SC: IC1.13 (SC2); also elsewhere on the board
/MUX3_SD: IC1.12 (SD2); also elsewhere on the board
/MUX4_SC: IC1.16 (SC3); also elsewhere on the board
/MUX4_SD: IC1.15 (SD3); also elsewhere on the board
/Main Mux to Thermistor Muxes/Address Jump/ADDR_0: IC1.1 (A0); also elsewhere on the board
/Main Mux to Thermistor Muxes/Address Jump/ADDR_1: IC1.2 (A1); also elsewhere on the board
/SCL: IC1.18 (SCL), R14.2, U3.1 (SCL); also elsewhere on the board
/SDA: IC1.19 (SDA), R13.2, U3.3 (SDA); also elsewhere on the board
/VREG: IC1.20 (VDD), R8.1, R9.1, R10.1, R11.1, R12.1, R13.1, R14.1, U3.4 (VCC); also elsewhere on the board
unnamed: IC1.4 (~INT0), R9.2
unnamed: IC1.7 (~INT1), R8.2
unnamed: IC1.11 (~INT2), R12.2
unnamed: IC1.14 (~INT3), R11.2
unnamed: IC1.3 (~RESET), R10.2

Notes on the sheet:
Power
REMOVED FROM BOARD
Keeping - I2C pullup resistors
Which leads to Mux 1 data out -> GPIO1 Mux 2 data out -> GPIO2 Mux 3 data out -> GPIO3 Mux 4 data out -> GPIO6
* pg. 8 Pull-up resistor
I2C Memory
(from MKV)
Connections to the DA board Thermistors Main Mux that connects to possible 4 other mux "modules"
pg. 6 Device Address
Each for one DA Module
Outward connections to + MUX1 SD + MUX1 SC + MUX2 SD + MUX2 SC + MUX3 SD + MUX3 SC + MUX4 SD + MUX4 SC
Inward connections to + Main BMS Chip SDA + Main BMS Chip SCL
Pull-up resistors for I2C Communcation
All temperatures routed to ADBMS1818 Chip


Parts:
C10: C_10nF; C_0603; MPN CL10B103KB8NNNC
F2: 200mA_Fuse; Fuse_1206_3216Metric; MPN 0466.200NRHF
JP2: SolderJumper_2_Open; SolderJumper-2_P1.3mm_Open_TrianglePad1.0x1.5mm
R17: 22R-1W; R_2512_6332Metric; MPN 352022RJT
R18: 10R; R_0603; MPN SG73P1JTTD100J

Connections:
/C17: C10.2, JP2.2 (B); also elsewhere on the board
/C18: C10.1, JP2.1 (A), R18.2; also elsewhere on the board
/CELL18: F2.1; also elsewhere on the board
/S18: R17.2; also elsewhere on the board
unnamed: F2.2, R17.1, R18.1

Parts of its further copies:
C9, C11, C12, C13, C14, C15, C16, C17, C18, C19, C20, C21, C22, C23, C24, C25, C26: C_10nF; C_0603; MPN CL10B103KB8NNNC
F1, F3, F4, F5, F6, F7, F8, F9, F10, F11, F12, F13, F14, F15, F16, F17, F18: 200mA_Fuse; Fuse_1206_3216Metric; MPN 0466.200NRHF
JP1, JP3, JP4, JP5, JP6, JP7, JP8, JP9, JP10, JP11, JP12, JP13, JP14, JP15, JP16, JP17, JP18: SolderJumper_2_Open; SolderJumper-2_P1.3mm_Open_TrianglePad1.0x1.5mm
R15, R19, R21, R23, R25, R27, R29, R31, R33, R35, R37, R39, R41, R43, R45, R47, R49: 22R-1W; R_2512_6332Metric; MPN 352022RJT
R16, R20, R22, R24, R26, R28, R30, R32, R34, R36, R38, R40, R42, R44, R46, R48, R50: 10R; R_0603; MPN SG73P1JTTD100J

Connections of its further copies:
/C1: C25.2, C26.1, JP17.2 (B), JP18.1 (A), R50.2; also elsewhere on the board
/C2: C24.2, C25.1, JP16.2 (B), JP17.1 (A), R48.2; also elsewhere on the board
/C3: C23.2, C24.1, JP15.2 (B), JP16.1 (A), R46.2; also elsewhere on the board
/C4: C22.2, C23.1, JP14.2 (B), JP15.1 (A), R44.2; also elsewhere on the board
/C5: C21.2, C22.1, JP13.2 (B), JP14.1 (A), R42.2; also elsewhere on the board
/C6: C20.2, C21.1, JP12.2 (B), JP13.1 (A), R40.2; also elsewhere on the board
/C7: C19.2, C20.1, JP11.2 (B), JP12.1 (A), R38.2; also elsewhere on the board
/C8: C18.2, C19.1, JP10.2 (B), JP11.1 (A), R36.2; also elsewhere on the board
/C9: C17.2, C18.1, JP9.2 (B), JP10.1 (A), R34.2; also elsewhere on the board
/C10: C16.2, C17.1, JP8.2 (B), JP9.1 (A), R32.2; also elsewhere on the board
/C11: C15.2, C16.1, JP7.2 (B), JP8.1 (A), R30.2; also elsewhere on the board
/C12: C14.2, C15.1, JP6.2 (B), JP7.1 (A), R28.2; also elsewhere on the board
/C13: C13.2, C14.1, JP5.2 (B), JP6.1 (A), R26.2; also elsewhere on the board
/C14: C12.2, C13.1, JP4.2 (B), JP5.1 (A), R24.2; also elsewhere on the board
/C15: C9.2, C12.1, JP1.2 (B), JP4.1 (A), R22.2; also elsewhere on the board
/C16: C9.1, C11.2, JP1.1 (A), JP3.2 (B), R16.2; also elsewhere on the board
/C17: C11.1, JP3.1 (A), R20.2; also elsewhere on the board
/CELL1: F18.1; also elsewhere on the board
/CELL2: F17.1; also elsewhere on the board
/CELL3: F16.1; also elsewhere on the board
/CELL4: F15.1; also elsewhere on the board
/CELL5: F14.1; also elsewhere on the board
/CELL6: F13.1; also elsewhere on the board
/CELL7: F12.1; also elsewhere on the board
/CELL8: F11.1; also elsewhere on the board
/CELL9: F10.1; also elsewhere on the board
/CELL10: F9.1; also elsewhere on the board
/CELL11: F8.1; also elsewhere on the board
/CELL12: F7.1; also elsewhere on the board
/CELL13: F6.1; also elsewhere on the board
/CELL14: F5.1; also elsewhere on the board
/CELL15: F4.1; also elsewhere on the board
/CELL16: F1.1; also elsewhere on the board
/CELL17: F3.1; also elsewhere on the board
/S1: R49.2; also elsewhere on the board
/S2: R47.2; also elsewhere on the board
/S3: R45.2; also elsewhere on the board
/S4: R43.2; also elsewhere on the board
/S5: R41.2; also elsewhere on the board
/S6: R39.2; also elsewhere on the board
/S7: R37.2; also elsewhere on the board
/S8: R35.2; also elsewhere on the board
/S9: R33.2; also elsewhere on the board
/S10: R31.2; also elsewhere on the board
/S11: R29.2; also elsewhere on the board
/S12: R27.2; also elsewhere on the board
/S13: R25.2; also elsewhere on the board
/S14: R23.2; also elsewhere on the board
/S15: R21.2; also elsewhere on the board
/S16: R15.2; also elsewhere on the board
/S17: R19.2; also elsewhere on the board
unnamed: F1.2, R15.1, R16.1
unnamed: F3.2, R19.1, R20.1
unnamed: F4.2, R21.1, R22.1
unnamed: F5.2, R23.1, R24.1
unnamed: F6.2, R25.1, R26.1
unnamed: F7.2, R27.1, R28.1
unnamed: F8.2, R29.1, R30.1
unnamed: F9.2, R31.1, R32.1
unnamed: F10.2, R33.1, R34.1
unnamed: F11.2, R35.1, R36.1
unnamed: F12.2, R37.1, R38.1
unnamed: F13.2, R39.1, R40.1
unnamed: F14.2, R41.1, R42.1
unnamed: F15.2, R43.1, R44.1
unnamed: F16.2, R45.1, R46.1
unnamed: F17.2, R47.1, R48.1
unnamed: F18.2, R49.1, R50.1

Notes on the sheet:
RDischarge
Leakage is ~4.8% of total capacity
Use in order to have less cell connections - short high rails together
"A cell pin filter of 100 Ω and 10 nF is recommended for all applications" ADBMS1818 datasheet pg. 71
This is a Hierarchical Sheet. That means that this is a "copy-paste" block for each block shown. (ie. As seen on "Voltage Filter")
CFilter
"Note that the antialiasing filter resistor is part of the discharge path and must be removed or reduced. Use of an RC for added cell voltage measurement filtering is permitted, but the filter resistor must remain small, typically around 10 Ω to reduce the effect on the balance current." pg. 72
Maximum Balance Resistor = Nominal Cell Voltage / Balance Current = 3.95V / 0.00028611111A = 13805.8253Ω
However, since it limits the balancing current...
Minimum Balance current [A] = (Max leakage [A] - Min leakage [A]) / (daily balancing time [hours] / 24 [hours]) = (4.020 Ah-3.814 Ah)/(30*24 hrs) = 0.00028611111 A = 0.28611111 mA
ADBMS1818 suggests that 5% leakage is a reasonable assumption
Jumper
Voltage Sense Overcurrent Protection (Fuse) Rule: EV.8.4.4
As long as balance current is below 200mA, everything is okay to use the internal MOSFETs of the ADBMS1818 chip for balancing. These are the calculated absolute minimums for balancing the Samsung 40T 21700s, but we can max up near where balance current is almost 200mA.
Filtering RC circuit as depicted on ADBMS1818 datasheet pg. 72
RFilter
Balance Current V = 3.95 V R = R_{DISCHARGE} + R_{FILTER} + R_{DS_ON} = 22 Ω + 10 Ω + 4 Ω = 36 Ω I = 3.95 V / 36 Ω = 0.10972222222222222 A = 109.72 mA Power P = I^2 R = (109.72 mA)^2 * 36 Ω = 0.43340277777 W
Cells: Samsung 40T 21700 https://cdn.shopify.com/s/files/1/0481/9678/0183/files/Samsung_Introduction_of_New_40T_v3.pdf?v=1612843210


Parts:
R57, R58: R_15k; R_0603; MPN WR06X153 JTL

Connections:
/MUX1_SC: R57.1; also elsewhere on the board
/MUX1_SD: R58.1; also elsewhere on the board
/VREG: R57.2, R58.2; also elsewhere on the board

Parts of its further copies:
R55, R56, R59, R60, R61, R62: R_15k; R_0603; MPN WR06X153 JTL

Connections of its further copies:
/MUX2_SC: R59.1; also elsewhere on the board
/MUX2_SD: R60.1; also elsewhere on the board
/MUX3_SC: R55.1; also elsewhere on the board
/MUX3_SD: R56.1; also elsewhere on the board
/MUX4_SC: R61.1; also elsewhere on the board
/MUX4_SD: R62.1; also elsewhere on the board
/VREG: R55.2, R56.2, R59.2, R60.2, R61.2, R62.2; also elsewhere on the board

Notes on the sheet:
I2C pull-up resistors
Optional placement on DA Modules instead
Using a hierarchical sheet for simplicity and so that resistor values are easy to replace
LTC1380 Datasheet pg. 3


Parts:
JP19, JP20: SolderJumper_3_Open; SolderJumper-3_P2.0mm_Open_TrianglePad1.0x1.5mm
R51, R52: R_4.99K; R_0603; MPN RMCF0603FT4K99

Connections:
/Main Mux to Thermistor Muxes/Address Jump/ADDR_0: JP19.2 (C); also elsewhere on the board
/Main Mux to Thermistor Muxes/Address Jump/ADDR_1: JP20.2 (C); also elsewhere on the board
/Main Mux to Thermistor Muxes/Address Jump/PULL_DOWN: JP19.3 (B), JP20.3 (B), R52.1
/Main Mux to Thermistor Muxes/Address Jump/PULL_UP: JP19.1 (A), JP20.1 (A), R51.2
/VREG: R51.1; also elsewhere on the board

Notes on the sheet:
Power
Only one resistor on at a time. Controls whether pull-up or pull-down.
I2C Address Setting Jumper

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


Board: 2 copper layers, 168.5 x 29.6 mm, 192 parts (4 on the bottom side), 117 nets.

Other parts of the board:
QR*****: hw.oem.to/6_BMS-CSC_1; QR_6_BMS-CSC_1
kibuzzard-63B4D82F: G***; kibuzzard-63B4D82F
kibuzzard-63B4D834: G***; kibuzzard-63B4D834
kibuzzard-63B4E58E: G***; kibuzzard-63B4E58E
kibuzzard-63B4E59A: G***; kibuzzard-63B4E59A
kibuzzard-63B4E581: G***; kibuzzard-63B4E581
kibuzzard-63B4E593: G***; kibuzzard-63B4E593
kibuzzard-63B4EB9B: G***; kibuzzard-63B4EB9B
kibuzzard-63B4EBA9, kibuzzard-63B4EBA9#2: G***; kibuzzard-63B4EBA9
kibuzzard-63B4EBAD, kibuzzard-63B4EBAD#2: G***; kibuzzard-63B4EBAD
kibuzzard-63B4EBB3, kibuzzard-63B4EBB3#2: G***; kibuzzard-63B4EBB3
kibuzzard-63B4EBB8, kibuzzard-63B4EBB8#2: G***; kibuzzard-63B4EBB8
kibuzzard-63B4EBF9: G***; kibuzzard-63B4EBF9
kibuzzard-63B4EC1B: G***; kibuzzard-63B4EC1B
kibuzzard-63B4EC4E: G***; kibuzzard-63B4EC4E
kibuzzard-63B4EC5B: G***; kibuzzard-63B4EC5B
kibuzzard-63B4EC6B: G***; kibuzzard-63B4EC6B
kibuzzard-63B4EC7A: G***; kibuzzard-63B4EC7A
kibuzzard-63B4EC20: G***; kibuzzard-63B4EC20
kibuzzard-63B4EC53: G***; kibuzzard-63B4EC53
kibuzzard-63B4EC66: G***; kibuzzard-63B4EC66
kibuzzard-63B4EC74: G***; kibuzzard-63B4EC74
kibuzzard-63B4EC80: G***; kibuzzard-63B4EC80
kibuzzard-63B4ED2A: G***; kibuzzard-63B4ED2A
kibuzzard-63B4ED25: G***; kibuzzard-63B4ED25
kibuzzard-63B4ED94: G***; kibuzzard-63B4ED94
kibuzzard-63B8E034: G***; kibuzzard-63B8E034
kibuzzard-63B8E079: G***; kibuzzard-63B8E079
kibuzzard-63BF4CDF: G***; kibuzzard-63BF4CDF
kibuzzard-63BF4D5E: G***; kibuzzard-63BF4D5E
kibuzzard-63BF5C8C: G***; kibuzzard-63BF5C8C
kibuzzard-63BF5C85: G***; kibuzzard-63BF5C85
kibuzzard-63BF465A: G***; kibuzzard-63BF465A
kibuzzard-6565800E: G***; kibuzzard-6565800E
kibuzzard-65658054: G***; kibuzzard-65658054

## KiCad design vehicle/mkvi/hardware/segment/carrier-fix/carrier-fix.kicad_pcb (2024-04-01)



Board: 2 copper layers, 282.1 x 29.6 mm, 6 parts (6 on the bottom side), 32 nets.

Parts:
J1: Automotive_M.2; MKVI_BMS_CSC
J2, J3: TST-108-01-T-D; TST-108-XX-T-D
J4, J4#2: MicroFit_RA_9x2
kibuzzard-65FD0D90: G***; kibuzzard-65FD0D90

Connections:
/CELL1: J1.56, J4.1
/CELL2: J1.57, J4.2
/CELL3: J1.58, J4.3
/CELL4: J1.59, J4.4
/CELL5: J1.60, J4.5
/CELL6: J1.61, J4.6
/CELL7: J1.62, J4.7
/CELL8: J1.63, J4.8
/CELL9: J1.64, J4.9
/CELL10: J1.65, J4.17
/CELL11: J1.66, J4.16
/CELL12: J1.67, J4.15
/CELL13: J1.68, J4.14
/CELL14: J1.69, J4.13
/CELL15: J1.70, J4.12
/CELL16: J1.71, J4.11
/CELL17: J1.36, J1.37, J1.72, J4.10
/GND: J1.4, J1.7, J1.10, J1.13, J1.16, J1.19, J1.43, J1.46, J2.14, J2.16, J4.18
/MUX1_SC: J1.18, J2.11
/MUX1_SD: J1.17, J2.13
/MUX2_SC: J1.15, J2.9
/MUX2_SD: J1.14, J2.12
/MUX3_SC: J1.12, J2.7
/MUX3_SD: J1.11, J2.10
/MUX4_SC: J1.9, J2.3
/MUX4_SD: J1.8, J2.6
/MUX_OUT_1: J1.6, J2.4
/MUX_OUT_2: J1.42, J2.8
/MUX_OUT_3: J1.5, J2.2
/MUX_OUT_4: J1.41, J2.5
/VREF2: J1.P38, J1.P39, J1.P40, J2.15
/VREG: J1.P1, J1.P2, J1.P3, J2.1

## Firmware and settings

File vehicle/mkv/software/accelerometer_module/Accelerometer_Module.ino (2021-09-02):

/*
 * Board: Accelerometer Module
 * Version: v1.0
 * Description: The goal of this board is to measure the frequency of vibrations in the chassis
 * in order to perform modal analysis.
 */

/****** Libraries ******/
#include <SPI.h>
#include <SD.h>
#include <Wire.h>

/****** LED Macros ******/
// Voltage Indicator LED
#define DDR_VLED DDRC
#define PORT_VLED PORTC
#define HIGH_VLED PC2
#define MED_VLED PC1
#define LOW_VLED PC0

// Status LED
#define DDR_SLED DDRD
#define PORT_SLED PORTD
#define ON_LED PD5
#define READY_LED PD6


/****** Button Macros ******/
#define BUTTON PD7
#define DDR_BUTTON DDRD


/****** SPI Macros ******/
#define MOSI PB3
#define MISO PB4
#define SCK PB5
#define DDR_SPI DDRB
#define PORT_SPI PORTB

// Accelerometer
#define ACC_CS PB2

#define READ 1
#define WRITE 0
#define MULTIPLE 1
#define SINGLE 0
#define RWbit 7 // Location of Read/Write Bit (Accelerometer)
#define MSbit 6 // Location of Multiple/Single Bit (Accelerometer)
#define WHOAMI 0x0F // Location if WHO AM I register (Accelerometer)
#define OUT_XL 0b101000 // Location of OUT_X_L (Accelerometer)
#define OUT_XH 0b101001 // Location of OUT_X_H (Accelerometer)
#define OUT_YL 0b101010 // Location of OUT_Y_L (Accelerometer)
#define OUT_YH 0b101011 // Location of OUT_Y_H (Accelerometer)
#define OUT_ZL 0b101100 // Location of OUT_Z_L (Accelerometer)
#define OUT_ZH 0b101101 // Location of OUT_Z_H (Accelerometer)

// SD Card
#define SD_CS PB1

/****** I2C Macros ******/
#define INA260_ADDR 1000000
#define VOLTAGE_REG 0x02

// Variable Declaration

void setup() {
  
  DDR_SLED |= _BV(READY_LED);
  DDR_BUTTON &= ~_BV(BUTTON);
  DDR_VLED |= _BV(HIGH_VLED);

  // Accelerometer CS Pin
  DDR_SPI |= _BV(ACC_CS);

  // Activate SD Card @ CS Pin
  // TODO: Check if PB1 can be used a select pin input for .begin() function
  SD.begin(SD_CS);

  // Activate I2C Communication
  Wire.begin();

  // Set SPI pins at Output
  DDR_SPI |= _BV(SCK) | _BV(MOSI);

  
//  PCICR |= _BV(PCIE2);
//  PCMSK2 |= _BV(PCINT23);
//  sei();
}

//ISR(PCINT2_vect) {
//  PORTD ^= _BV(PD6);
//}

void loop() {
  int xyzData[6]; // initalize memset

  // QUESTION: Do I need this if I initalize the variable in every loop?
  memset(xyzData,0,6); // set xyzData to zeros

  // get accelerometer data
  for (int i = 0; i < 6; i++) {
    xyzData[ i ] = getData(READ, SINGLE, (OUT_XL + i), ACC_CS);
  }

  // creates/opens file "data.txt"
  // starts writing at END of file
  File data = SD.open("data.txt", FILE_WRITE);
  if (data) {
    for ( int i = 0; i < 3; i++ ) {
      data.println(xyzData[ i*2 ] >> 6 | xyzData[ (i*2)+1 ] << 2);
    }
    data.println("");
    data.close();
  }
  
  // I2C Slave Address (INA260) -- 1000000
  // Bus Voltage register (0x02)
  // Alert Limit register (0x07)
  Wire.beginTransmission(INA260_ADDR);
  Wire.write(byte(VOLTAGE_REG));
  Wire.endTransmission();
  Wire.requestFrom(INA260_ADDR, 16);
  int voltage = 0b0;
  while (Wire.available()) {
    int data = Wire.read();
    // Will the data come in the right order to collect it like this?
    voltage = (voltage << 1) | data;
  }
  
  if (bit_is_set( PINB, PB1 )) {
    PORT_SLED ^= _BV(READY_LED);
    delay(1000);
  }
}

int getData(int rwbit, int msbit, int address, int cs) {
  // Accelerometer Datasheet - Max Speed 1MHz
  // Page 27 - SPI MODE 0 - Output on Falling Edge, Data Capture on Rising Edge
  
  SPI.beginTransaction(SPISettings(400000, MSBFIRST, SPI_MODE0));
  PORT_SPI &= ~_BV(cs);
  int output = SPI.transfer(rwbit << RWbit | msbit << MSbit | address);
  PORT_SPI |= _BV(cs);
  SPI.endTransaction();
  return output;
}

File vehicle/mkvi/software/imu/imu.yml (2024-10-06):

name: imu
publish:
  - name: imu_accel
    id: 0x430
    freq_hz: 100
    signals:
      - name: accel_x
        slice: 0 + 16
        unit:
          type: uint16_t
          name: ""
          scale: 1
          offset: 0
      - name: accel_y
        slice: 16 + 16
        unit:
          type: uint16_t
          name: ""
          scale: 1
          offset: 0
      - name: accel_z
        slice: 32 + 16
        unit:
          type: uint16_t
          name: ""
          scale: 1
          offset: 0
  - name: imu_gyro
    id: 0x431
    freq_hz: 100
    signals:
      - name: gyro_x
        slice: 0 + 16
        unit:
          type: uint16_t
          name: ""
          scale: 1
          offset: 0
      - name: gyro_y
        slice: 16 + 16
        unit:
          type: uint16_t
          name: ""
          scale: 1
          offset: 0
      - name: gyro_z
        slice: 32 + 16
        unit:
          type: uint16_t
          name: ""
          scale: 1
          offset: 0
  - name: imu_magnet
    id: 0x432
    freq_hz: 100
    signals:
      - name: magnet_x
        slice: 0 + 16
        unit:
          type: uint16_t
          name: ""
          scale: 1
          offset: 0
      - name: magnet_y
        slice: 16 + 16
        unit:
          type: uint16_t
          name: ""
          scale: 1
          offset: 0
      - name: magnet_z
        slice: 32 + 16
        unit:
          type: uint16_t
          name: ""
          scale: 1
          offset: 0

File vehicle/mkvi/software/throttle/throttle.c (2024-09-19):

#include "libs/adc/api.h"
#include "libs/can/api.h"
#include "libs/gpio/api.h"
#include "libs/timer/api.h"

#include "throttle_config.h"
#include "vehicle/mkvi/software/throttle/can_api.h"

#include <avr/interrupt.h>
#include <math.h>
#include <stdbool.h>
#include <stdint.h>
#include <stdlib.h>
#include <sys/types.h>
#include <util/delay.h>

// commented out temporarily for Jack's testing
#include "projects/btldr/btldr_lib.h"
#include "projects/btldr/git_sha.h"
#include "projects/btldr/libs/image/api.h"

/*
 * Required for btldr
 */
image_hdr_t image_hdr __attribute__((section(".image_hdr"))) = {
    .image_magic = IMAGE_MAGIC,
    .git_sha = STABLE_GIT_COMMIT,
};

/*
 * Sets the torque request in the motor controller command message
 */
#define SET_TORQUE_REQUEST(torque) \
    (m192_command_message.torque_command = (torque))

#define MIN(a, b) (((a) < (b)) ? (a) : (b))
#define MAX(a, b) (((a) > (b)) ? (a) : (b))

// all possible throttle states
enum State {
    THROTTLE_IDLE,
    THROTTLE_RUN,
    THROTTLE_L_OUT_OF_RANGE,
    THROTTLE_R_OUT_OF_RANGE,
    THROTTLE_POSITION_IMPLAUSIBILITY,
    THROTTLE_BRAKE_PRESSED
};

struct throttle_state_s {
    volatile bool send_can;
    uint16_t implausibility_fault_counter;
    bool brake_pressed;
} throttle_state = { 0 };

void timer0_isr(void) {
    throttle_state.send_can = true;
}

volatile bool run_1ms = false;

void timer1_isr(void) {
    run_1ms = true;
}

static void pcint0_callback(void) {
    throttle.ss_is = !gpio_get_pin(SS_IS);
}

/*
    Read value from throttle potentiometer, maps it to value between 0 and
    255 where 255 = 100% throttle
    Takes in bool for whether the read throttle is the left or not for
    debugging purposes
    Returns an int16_t representing pedal travel
*/
static int16_t get_throttle_travel(const throttle_potentiometer_s* throttle,
                                   bool is_left_throttle) {
    int16_t throttle_raw = adc_read(throttle->adc_pin);
    if (is_left_throttle) {
        throttle_debug.throttle_l_raw = throttle_raw;
    } else {
        throttle_debug.throttle_r_raw = throttle_raw;
    }
    throttle_raw >>= 2; // TODO: ask why this is here
    int16_t range = throttle->throttle_max - throttle->throttle_min;
    float position_pct
        = (float)(throttle_raw - throttle->throttle_min) / (float)range;
    return floor(position_pct * MAX_THROTTLE_POS);
}

/*
    Check if sensors return a value out of range (<0 or >255)
    Args:
        pos_l: int16_t sensor value of throttle pot 1eft
        pos_r: int16_t sensor value of throttle pot right
    Returns:
        implausibility: boolean if throttle out of range or not
*/
static bool check_out_of_range(int16_t* pos_l, int16_t* pos_r) {
    bool implausibility = false;

    // Check 1st pot
    if (*pos_l > MAX_THROTTLE_POS) {
        *pos_l = MAX_THROTTLE_POS;
        throttle.throttle_status = THROTTLE_L_OUT_OF_RANGE;
        throttle_debug.throttle_l_out_of_range = true;
        implausibility = true;
    } else if (*pos_l < MIN_THROTTLE_POS) {
        *pos_l = MIN_THROTTLE_POS;
        throttle.throttle_status = THROTTLE_L_OUT_OF_RANGE;
        throttle_debug.throttle_l_out_of_range = true;
        implausibility = true;
    } else {
        throttle_debug.throttle_l_out_of_range = false;
    }

    // Check 2nd pot
    if (*pos_r > MAX_THROTTLE_POS) {
        *pos_r = MAX_THROTTLE_POS;
        throttle.throttle_status = THROTTLE_R_OUT_OF_RANGE;
        throttle_debug.throttle_r_out_of_range = true;
        implausibility = true;
    } else if (*pos_r < MIN_THROTTLE_POS) {
        *pos_r = MIN_THROTTLE_POS;
        throttle.throttle_status = THROTTLE_R_OUT_OF_RANGE;
        throttle_debug.throttle_r_out_of_range = true;
        implausibility = true;
    } else {
        // Will be reset if Ready to Drive is not on
        throttle.throttle_status = THROTTLE_RUN;
        throttle_debug.throttle_r_out_of_range = false;
    }
    return implausibility;
}

/*
    Check for deviation between 2 throttle sensors, >10% deviation is an
    implausibility
    Args:
        pos_min: int16_t bigger sensor value of the 2 throttle pots
        pos_max: int16_t smaller sensor value of the 2 throttle pots
    Returns:
        boolean if there's deviation or not
*/
static bool check_deviation(int16_t pos_max, int16_t pos_min) {
    if (pos_max - pos_min > APPS_IMPLAUSIBILITY_DEVIATION_THRESHOLD) {
        throttle.throttle_status = THROTTLE_POSITION_IMPLAUSIBILITY;
        throttle_debug.throttle_deviation = true;
        return true;
    } else {
        throttle.throttle_status = THROTTLE_RUN;
        throttle_debug.throttle_deviation = false;
        return false;
    }
}
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

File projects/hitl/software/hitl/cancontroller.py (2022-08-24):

# Base python
import threading
from typing import Callable
import logging
from collections import defaultdict

# Extended python
import cantools
import can

# Project Imports
from utils import artifacts_path, get_logging_config


class CANController:
    """High level python object to interface with hardware.

    The CANController works **passively** for reading signals; you create one with a path to a DBC, and it keeps track of all states automatically

    Args:
        can_spec_path (str): Path to CAN spec. Should be a ``.dbc`` file.
        bustype (str): CAN bustype to use. Dependant on hardware - see OEM CAN documentation for more info
        channel (str): CAN channel to use. Dependant on hardware - see OEM CAN documentation for more info
        bitrate (int): Bitrate of CAN bus. Defaults to 500Kbps, which shouldn't change for most work on our team

    Args are pulled from artifacts/config.ini but can be manually specified as well
    """

    def __init__(
        self,
        can_spec_path: str = "vehicle/mkv/mkv.dbc",
        bustype: str = "socketcan",
        channel: str = "vcan0",
        bitrate: int = 500000,
    ):
        # Create logger
        get_logging_config() 
        self.log = logging.getLogger(name=__name__)

        # Create empty set of periodic messages
        self.periodic_messages = {}

        # Set up dictionary of messages
        self.message_of_signal, self.signals = self._create_state_dictionary(
            can_spec_path
        )

        try:
            self.can_bus = can.interface.Bus(
                channel=channel, bustype=bustype, bitrate=bitrate
            )
            self.kill_flag = threading.Event()
            listener = threading.Thread(
                target=self._listen,
                name="listener",
                kwargs={
                    "can_bus": self.can_bus,
                    "callback": self._rx_callback,
                    "kill_flag": self.kill_flag,
                },
            )
            listener.start()
        except OSError as e:
            raise

    def get_state(self, signal):
        """
        Get the state of a can signal on the car

        Args:
            signal (str): signal name to get
        """
        try:
            msg = self.message_of_signal[signal]
        except KeyError:
            raise Exception(f"Cannot get state of signal '{signal}'. It wasn't found.")

        self.log.debug(f"Fetched signal {signal} as {self.signals[msg][signal]}")
        return self.signals[msg][signal]

    def set_state(self, signal, value):
        """
        Set the state of a can signal on the car

        Args:
            signal (str): Signal name to set
            value (varying types): Decoded value to set signal to

            Note: Decoded includes all of the decoding instructions in the DBC
            So any fault/state enum signals would use the actual name, like "PRECHARGE"
            Shutdown Sense signals would be "OPEN" or "CLOSED"
            Any values that have offsets or scales should have those applied, 
                so for example for throttle potentiometers we would use the percentages,
                not the raw values
        """
        try:
            msg_name = self.message_of_signal[signal]
        except KeyError:
            raise KeyError(f"Cannot set state of signal '{signal}'. It wasn't found.")

        msg = self.db.get_message_by_name(msg_name)

        # Update internal dictionary
        self.signals[msg_name][signal] = value

        # Encode data and create message
        data = msg.encode(self.signals[msg_name])
        message = can.Message(
            arbitration_id=msg.frame_id, data=data, is_extended_id=False
        )

        # Send message
        if msg_name in self.periodic_messages:
            self.periodic_messages[msg_name].modify_data(message)
        else:
            self.can_bus.send(message)

        self.log.debug(f"Set signal {signal} to {value}")

    def set_periodic(self, msg_name, period):
        """
        Set a message to be send periodically, at a specified period in seconds

        All states in the message should be set before starting a periodic broadcast,
        though they can be changed without interrupting the periodic broadcast.

        Args:
            msg_name (str): The name of the message to send periodically
            period (float): Period of seconds between each message
        """
        if msg_name not in self.signals:
            raise KeyError(f"Message {msg_name} not found in messages.")

        if msg_name in self.periodic_messages:
            raise Exception(f"Message {msg_name} is already being sent periodically.")

        msg = self.db.get_message_by_name(msg_name)

        # Encode message data and create message
        data = msg.encode(self.signals[msg_name])
        message = can.Message(
            arbitration_id=msg.frame_id, data=data, is_extended_id=False
        )

        # Send message
        send_task = self.can_bus.send_periodic(message, period)
        self.periodic_messages[msg_name] = send_task

        self.log.debug(f"Set {msg_name} to be sent periodically every {period} ms")

    def stop_periodic(msg_name: str):
        """
        Stop a periodic message task
        """
        if msg_name in self.periodic_messages:
            self.periodic_messages[msg_name].stop()
            del self.periodic_messages[msg_name]
            self.log.debug(f"Stopped periodic sending of {msg_name}")
        else:
            self.log.error(f"Message {msg_name} is not being sent periodically")

    def stop_all_periodic(self):
        """
        Stop all periodic message tasks
        """
        self.can_bus.stop_all_periodic_tasks()
        self.log.debug("Stopped all periodic tasks")

    def _create_state_dictionary(self, path: str):
        """Generate self.message_of_signal and self.signals

        Args:
            path (str): Path to CAN spec file (DBC)
        """
        # Create database that has all the messages in the dbc file in type message
        self.db = cantools.database.load_file(path)

        # Iterates through messages to create state dictionaries
        message_of_signal = {}
        signals = defaultdict(dict)
        for msg in self.db.messages:
            for sig in msg.signals:
                signals[msg.name][sig.name] = 0
                message_of_signal[sig.name] = msg.name

        return message_of_signal, signals

    def _rx_callback(self, msg):
        """
        Callback function to the listener thread.

        Parses through a CAN frame and updates the self.states dictionary
        """
        # Get the message name
        msg_name = self.db.get_message_by_frame_id(msg.arbitration_id).name
        # Decode the data
        data = self.db.decode_message(msg.arbitration_id, msg.data)
        # Update the state dictionary
        self.signals[msg_name].update(data)
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

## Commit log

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2021-09-23 Fix KiCad net label issues (#42)
    An issue arose when people didn't have the clean/smudge filters installed and that leaked KiCad issues into main.
    [air_control.sch, bms_core.sch, connectors.sch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]
2021-09-24 Updates based on feedback from @corey @adi_s to LV BMS tester board (#44)
    * Updates based on feedback to LV BMS tester board
    Also fixes smudge/clean
    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
    [lv_bms_tester_board.kicad_pcb, lv_bms_tester_board.sch]
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2021-10-05 Fixed template board (#55)
    * Added meta folder for adding kicad template board and renamed files to template_board
    * fixed name
    [template_board.kicad_pcb, template_board.sch]
2021-10-16 Update BSPD for MKV Wheels Spin (#45)
    * added test points, fixed broken net
    * Fix rescued parts
    * Small wording tweaks in schematic
    [bspd_brakelight.kicad_pcb, bspd_brakelight.sch]
2021-10-16 Fix silkscreen on Sensing Controller. (#58)
    * Increase power plane size.
    Increase the size of the 5.5V and 3.3V power planes.
    * Add test points.
    Add test points for PM/SM Miso/Mosi/CS.
    * Add front/left sense test points.
    * Make silkscreen legible.
    * Remove rescue lib
    * Remove Gerber zip file from output
    * Buildifer
    [connectors.sch, micros.sch, power.sch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]
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2021-10-21 Fix accumulator interface internal connector nets (#46)
    * fixed pinout on internal accumulator interface board
    * Add no-connects
    Reviewed by Corey (@coreyacl)
    [internal_interface.kicad_pcb, internal_interface.sch]
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2021-11-02 CANController Refactor (#62)
    * First pass at CANController refactor
    * Make IOController more forgiving for devices with incomplete setups
    * Fix setup.py
    [cancontroller.py]
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2021-11-15 Update BSPD/Brakelight code to use new libraries (#68)
    * Update BSPD code for new rev
    * Add BUILD file
    * Add config.h file
    * Update BSPD code to use new libraries
    * Fix BSPD code interrupts
    * Rename config.h to bspd_config.h
    [bspd_config.h]
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2021-11-30 fix: make AIR+ and AIR- boards rules compliant (#74)
    * fix: adjust routing to provide proper TS/GLVS separation of 4mm
    fix: reposition components to fix issues with parts on both sides
    fix: adjust sizing of relay model
    feat: add footprint for resistor
    * fix: move dimension to be visible
    * fix: add BUILD files for Bazel
    * fix: remove rescue libraries
    * fix: correct format for BUILD files
    [R_SMD_5329.STEP, air_minus.kicad_pcb, air_minus.sch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]
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2022-01-25 fix: update 3D model paths for monorepo (#70)
    * fix: update 3D model paths for monorepo
    * docs: typo fix
    * fix: remove references to old repo in pcbs
    [accelerometer.kicad_pcb, bms_core.kicad_pcb, bms_peripheral.kicad_pcb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]
2022-01-25 Enable periodic CAN message broadcasts (#85)
    * Add set_periodic function to cancontroller
    * fixup
    * periodic send test
    [cancontroller.py]
2022-01-27 Add missing BUILD files for MKV hardware (#76)
    * Remove images
    * Add missing BUILD files
    * Update BUILD files and remove PDFs
    * Fix all files with spaces in the name
    * Fix github workflow for files with spaces
    * Remove bms core resuce
    [CAN_Transceiver.fcstd, CAN_Transceiver.step, LED_0805_Base_GREEN001_sp.step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]
2022-01-28 microhitl python wrapper for pyserial (#90)
    * package for arduino serial comands
    * added arduino file
    * cleaned up code and restructured
    * removing deps
    * formatting
    * formatting
    * formatting
    * File restructure and updated BUILD file
    * cleaned up functions and added exception
    * formatting
    * updated fixes
    * minor comment fix
    * Move arduino file
    [microhitl.ino, microhitl.py]
2022-02-01 Add bazel options to build hitl library and run hitl setup script (#51)
    * Add bazel options to build hitl library and run hitl setup script
    * lint
    * Add missing bazel integrations
    * Buildifier
    * Fix WORKSPACE issue
    * Fix missing file build error
    * Fix imports for failing tests
    * Resolve missing singal type for ERROR signal
    * Add missing USB dependency in BUILD file
    * Remove incomplete rows in pin_info to avoid errors
    * Set default harness state to not real
    * squash
    * squash
    * Update tests to only run with physical hardware
    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
    [pin_info.csv]
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2022-02-24 Add service section controller hardware (#75)
    * made layout changes
    added space between components and arranged functional blocks on layout.
    * added traces to layout
    * added more traces
    * Added more traces
    Imported DXF file and finished traces. Need to add more labels for the
    test points + go through design checklist.
    * added 23.7 kOhm resistor, 12V_ power symbols
    * incorporated feedback from dr
    * complete service section controller layout, need to change some test point labels though
    * finalized service section pcb layout, added connector silkscreen labels
    * fixed a disconnect
    * checked that sizing is under 6.25x6.25
    * added title and name to schematic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
    [air_control.sch, bms_core.sch, connectors.sch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]
2022-03-24 Arturo/sensing controller layout (#124)
    * Add new inAmp for strain gauge.
    * Add buffers for voltage references.
    * Add parts to formula lib.
    * Get rid of rescue parts.
    * Add missing parts and do strain gauge layout.
    * Create functional blocks for sensing layout.
    * Adding Sensing Controller Layout (WPI)
    Adding the project, pcb, and schematic files. PCB layout only separated
    into blocks (12/17)
    * Add footprints/models for LDO and L8.1uF.
    * Adds LDO in PCB and Layout Draft
    Adds LDO and layout draft as of 2/22/22, where most connections besides
    the suspension strain have been realized, and a rough arrangement for
    suspension strain laid.
    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
    [DRV0006A.stp, IND_XAL4020_4X4_COC.step, micros.sch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]
2022-03-25 Add HitL primary board hardware (#99)
    * Add updated schematic, and parts over from OEM preffered parts
    * Swapped out out of stock analog mux. First pass at floor planning
    * replaced ADC and micromatch. Add 0-ohm resistors to power
    * Update passives. Update floorplan
    * Adding to layout. Fixed footprint for analog mux
    * add build file
    * fix build file...hopefully
    * rename file structure
    * minor changes
    * Layout in progress. Need to add differential pairs
    * first rev layout
    * add first pass silkscreen
    * rev 1 layout changes
    * add tespoints. export gerbs
    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
    [21-0040_A364_MXM.step, 5745781-4.step, 7-338069-6.step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]
2022-03-27 Telemetry Core (#66)
    * Add Telemetry Core incl. debugging leds, test points, 20-pin connector
    * fix: Rename telemetry core directory to all lowercase
    * fix: Rename kicad hardware to telemetry core
    * feat: add JST-GH 6-pin Connector to library
    * add spi rtc meant for telemetry core board
    * fix: change schematic symbol to be smaller and have background color
    * fix: small changes to schematic symbol
    * add: 32.768Hz Crystal
    * feat: set up schematic for rtc and add crystal
    * fix: rename symbol and footprint for JST connector
    * fix: rename 3D model file to no parentheses
    * fix: update schematic symbol ref for JST connector
    * feat: connect rxd and txd for radio,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
    [C_10pf.step, C_radial_10mm_5mm.step, JTX310_32.768KHZ--3DMode.STEP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]
2022-03-27 Go Kart BMS Core (#116)
    * feat: rev1 go kart BMS schematic
    * format: update BUILD file and rename project
    * fix: use proper gokart directory
    * feat: add shutdown sense
    fix: add missing labels
    * feat: rev1 layout of BMS, minor pin changes
    * fix: update connectors
    fix: update broken 3D model paths in library
    fix: use in stock transformer
    feat: new fan PWM circuit
    feat: add P-type transistor to parts library
    * feat: redo layout to incoporate updates & cleanup
    [bms_core.kicad_pcb, bms_core.sch]
2022-03-27 Add go-kart motor controller interface board (#119)
    * gokart mc ctrl first pass, codeword:AIRS
    * build + better directory structure
    * dir & project rename
    * added support for hall effect sensor
    * forgot label on PCINT0
    * oops MC parts
    * nearly complete first pass layout
    * needs silkscreen update, but rev1 complete
    * fixed ss
    * layout rev1, updates & fixes
    * updates, shipipng gerbers now
    * Fix issue in BUILD file
    * Fix rescue lib
    [motor_ctrl_interface.kicad_pcb, motor_ctrl_interface.sch]
2022-03-31 Updates to accumulator interface for cooling fans (#126)
    * delete this commit
    * add cooling and bspd nets to acc interface
    * Add layout changes and footprints
    * Updates to interface boards from Corey
    * Undo service section controller changes
    * Delete STEP file
    * ampseal pinout change + add ultrafit
    * polish and fix silkscreen
    * final rev. gerbs out
    * Remove STEP files from git
    * Fix merge conflicts
    * Remove rescue libs
    [430452400.stp, internal_interface.kicad_pcb, internal_interface.sch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]
2022-04-05 Add AIR Control code (#91)
    * Initial state machine
    * Initial new AIR code
    * Add unfinished state diagram and some code
    * Update state machine with enums
    * Create new AIR control code files
    * WIP
    * Remove old state machine library
    * Refactor state machine into 1ms task
    * Add code for new CAN address space
    This won't be merged in, I just wanted to try writing some code and want
    to commit it so that it exists in my repository.
    * Update fault list
    * Set state variable to match CAN message
    * Update AIR control code with new CAN API
    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
    [air.c, air_config.h]
2022-04-06 Add Go-Kart Throttle Schematic + Layout (#129)
    * initial commit
    * first pass at schematic
    * bypass caps and dnp resistors
    * start button and ready to drive light
    * change vout1 pin and connector power
    * rev 2complete
    * move connectors
    * add gerber
    * finished layout
    * clean up files
    * moved to single gokart folder
    * initial commit
    * first pass at schematic
    * bypass caps and dnp resistors
    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
    [throttle.kicad_pcb, throttle.sch]
2022-04-13 Add support for ATMega64m1 (#132)
    * Add support for ATMega64m1
    * Add 64m1 linker script
    * Add in support to libraries for 64m1
    * Fix UART BUILD
    * Add more expressive platforms for hardware
    * Move multiplatform jobs to matrix
    * Fix issue in GitHub Actions yml
    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
    [air_config.h]
2022-04-13 Add firmware test board (#127)
    * Fix layout draft
    * Update labels of microcontroller and connector
    * Delete rescues and clean up with git filters
    * Second layout draft of tester board
    * Add silkscreen and test points to draft 2
    * Add rear silkscreen
    * Add quick changes from round 2 feedback
    * Add GPIO inline resistors
    * Fix rescue libraries
    * Final tweaks to schematic and layout
    [firmware_tester_board.kicad_pcb, firmware_tester_board.sch]
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2022-04-18 Add BMS firmware (#107)
    * Add initial LTC6811 files from Linduino
    * Updated names and integrated with Bazel
    * Integrate SPI library to ltc6811
    * Clean up LTC6811 libraries and format
    * Update a few outdated things
    * Begin work on new BMS image
    * Add mux code
    * Add ATmega64m1 target for Bazel
    * Add CAN message support for voltage sensing
    Temp sensing is still WIP
    * Add under/over voltage checks in voltage task
    * Add fault state checking for initial_checks
    * Add BMS YML file to MKV BUILD
    * fmt
    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
    [bms.c, bms_config.c, bms_config.h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]
2022-04-18 Add updated MKV throttle code (#123)
    * Add throttle config and BUILD.
    * Recover YAML file
    * it compiles but does it work. does it even make sense
    * Add fixed logic
    * Fix build issue
    * Fix brake pluasibility check
    * Add comments for rules
    * Fix non-returning function
    * Updates based on Wenstrup's comments
    * Fixed timer and can sending
    * Updates to fix ADC issue
    * fixed ADC lib issue
    * fixes for throttle testing
    * second round of throttle testing - states, shutdown sense
    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
    [throttle.c, throttle_config.h]
2022-04-18 fix: update footprint for 100H inductor (#118)
    fix: update layout to match schematic of buck converter
    [template_board.kicad_pcb, template_board.sch]
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2022-05-14 Milestone: MKV Wheels Spinning (#135)
    * Remove BMS_SENSE from air control
    * Update calculation of pack voltage
    * Add debug LED to BSPD to show brake pressed
    * Fix inverted logic issue in bspd shutdown sensing
    * Update throttle debug message ID
    * Fix temperature CAN sending in BMS
    * Fix AIR check during SS_CLOSED
    * Fix BMS voltage comparison value in AIR control
    * Fix get_bms_voltage processing logic
    * Calibrate throttle and fix bugs (#140)
    * fixed state setting, calibrated pots
    * Clean up and add comments
    * Modify BMS temperature to use asynchronous architecture (#141)
    * Remove old comm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
    [R_TSMP.step, Relay_3350.step, Relay_5500.step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]
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2022-07-14 KiCad 6 :tada: :tada: :tada: (#151)
    * chore: migrate parts library to kicad 6
    * feat: switch kibot to kicad 6
    * chore: migrate projects to kicad 6
    * chore: remove legacy files
    * chore: remove legacy cache.lib
    * chore: remove rescue libraries
    * fix: correct 3D model paths where possible
    * chore: annotate migrated schematics
    * feat: remove legacy project filter
    * fix(bazel): update config for new project structure
    * fix(git): unignore external interface
    * fix: misc tweaks to resolve kibot errors
    [194270032.step, ADC.kicad_sch, ADC.sch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]
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2022-08-29 Added configurable CAN mask to CAN API (#165)
    * updated c file generation with configurable mask
    * updated test file to reflect configurable mask change
    * added unit test to fix mask config
    * linted code
    * revises mask dict generation for readability
    * revised mask dict generation for readability
    * added error handling for mismatching messages
    * updated test yaml info
    * fixed expected mob in test file
    * removed unnecessary import
    * updated error catching for unknown subsriptions
    * lint fixes
    * changed ValueError to warning
    * Revert "lint fixes"
    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
    [utils.py]
2022-09-12 Integrate CAN Software Update (#36)
    * Integrate shared memory library
    * Add crc32 library
    * Add flash library
    * Add image library
    * buildify
    * Add more comments and fix APIs
    * Clang-format and fix unused
    * --wip-- [skip ci]
    * Add initial bootloader client code
    * Initial CAN Software Update Client code
    * Add a bunch of files
    * Integrate Bazel into bootloader
    * Add ability to flash bootloader and patch header
    * Fix build issues with patched binary
    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
    [air.c, air_config.c, bms.c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]
2022-10-27 Add M.2 Footprint and Board Examples (#175)
    * Initial M.2 implementation
    * Add initial version of m.2 connector footprint
    * Add initial schematic and layout for daughter board
    * feat: example m.2 module
    * fix: update BUILD, remove files
    * fix: move header to better location
    * feat: arduino-esque motherboard
    * fix: chamfer edges
    * fix: swap SCK to not go through vias
    * feat: set board color to black
    * fix: bump power track width, adjust routing of 5V around connector
    [m.2_daughter.kicad_pcb, m.2_daughter.kicad_sch, m.2_motherboard.kicad_pcb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]
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2022-11-09 Hardware-in-the-loop primary rev 1.1 (#172)
    * Split schematic into sheets
    * Switch FTPROG to button and update I2C level shifter
    * Fix footprint for FTDI chip
    * Replace zero-ohm resistors with solder jumpers
    * Changes from feedback
    [ADC.kicad_sch, Micro8_PCA9517.step, ScrewTerminal_1x3.stp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]
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2022-12-09 Removing case duplicates part two, electric boogaloo! (#202)
    * Actually deleted SOD-923.step this time
    * Actually deleted Olin_O.kicad_mod this time
    * Revert "Renamed micromatch_female_ra_20 to Micromatch_Male_RA_20 because this is the male side of the connector named incorrectly."
    Going to take another crack at this rename. Looks like I did it wrong and deleted one of the folders entirely.
    This reverts commit 3bb458edd1b899bb2e14319e04d6dd3b10197030.
    * Actually renamed micromatch_female_ra_20 to Micromatch_Male_RA_20 because it was a male connector named incorrectly. This replaces the commit I just reverted.
    [Micromatch_Female_RA_20.fcstd, Micromatch_Female_RA_20.step, SOD-923.step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]
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2022-12-22 Add IMD latch board layout (#180)
    * Layout First Draft
    * Layout changes
    * Layout edge fix
    * PCB Layout Fixes
    * Silkscreen fix
    * Test point labels
    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
    [imd_latch.kicad_pcb, imd_latch.kicad_sch]
2022-12-23 AIR Control Layout (#189)
    * Initial version of AIR Control schematic
    * Removed obsolete parts, cleaned up schematic
    * Add M.2 Footprint and Board Examples (#175)
    * First review v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
    [AIRs.kicad_pcb, AIRs.kicad_sch, CAN_TCVR.kicad_sch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]
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2022-12-26 Add enum generation to CAN API (#170)
    * Add enum generation to CAN API
    * Fix issue with CAN generation and old syntax
    * Address PR feedback
    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
    [air.c, bms.c]
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2022-12-26 BSPD PCB Update (#204)
    * first draft of schematic
    * Updated Brakes Board
    * Revised a bit of the brakes board
    * try 2
    * updates from LV design check
    * edit BUILD file to add heirarchical (eek spelling?) files
    * response schematic after reviews
    * BUILD file update
    * fix bazel build
    * got rid of extra files
    * added PCB board layout and updated schematic
    * added some coolish silkscreen stuff and responded to jack's comments
    * forgot board name
    * added seperate buttons for brakelight and 5kW overrides
    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
    [Connector.kicad_sch, brakeLight.kicad_sch, brakes.kicad_pcb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]
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2023-01-11 Add MKVI roadkill harness (#198)
    * Initial commit for RKH schematic
    * Updates
    * Continue adding connections
    * Add analog multiplexing
    * Misc updates
    * Checkpoint
    * Add potentiometer footprint
    * Checkpoint
    * Spec out inductor
    * Add raspberry pi connector and more M.2 connections
    * Update and fix BUILD file
    * Checkpoint
    * Add more to layout
    * Layout checkpoint, might redo
    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
    [100SP1T1B4M2QE.step, G6L-1P_DC5.step, air_control.kicad_sch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]
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2023-02-27 Finalize boards for fab (#217)
    * add BOM tool to join BOMs
    * add custom BOM script for working with custom BOM fields
    * add patched QR plugin for better QR codes
    * add logo and authors to boards
    * update parts library and fix misc issues
    * migrate projects to new parts library
    [17-thermistor-7-probe.kicad_sch, 20-thermistor-group-4-probes.kicad_sch, 24-thermistor-group.kicad_sch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]
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2023-03-07 Add MKVI Nostril Motherboard (#209)
    * nostril mobo schematic 1st pass
    * remove unused files
    * add power/gnd for brake pressure
    * address PR feedback
    * update dashboard pinout
    * annotated schematic
    * first pass at schematic + layout
    * update silkscreen and add CAN term
    * final touches
    * Commit Rev 2; Respond to PR feedback
    * fix nostril dimensions
    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
    [ampseal23_RA.STEP, buck.kicad_sch, nostril.kicad_pcb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]
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2023-04-19 Python client for btldr (#186)
    * Initial commit
    * Fill in methods for python client
    * Refactor to include on-the-fly DBC
    * Refactor so that btldr DBC only uses offsets
    * Refactor and add more to flash method
    * Add CLI and move tests to separate folder
    * Add initial Python CLI for updatr
    * Remove accidentally-added throttle backup
    * Remove updatr DBC file generation (might re-add later)
    * Format python
    * Add back test binary file
    * Fix tests
    * Trigger build
    * Format again
    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
    [btldr.py, btldr_database.py, cli.py]
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2023-05-01 Fix issues with hardware filtering (#241)
    * Fix issues with hardware filtering
    * Fmt
    [btldr.py]
2023-09-02 KiCAD 7 CLI Update (#224)
    * small test pcb change
    * started
    * Switching Kibot to Kicad 7
    * Fixed all errors
    * Revert "small test pcb change"
    This reverts commit 8684a29d87f8170850efcf9ba644541f0bce3b16.
    Removing unnecessary PCB changes
    * Fixed Directory & Digital Ocean Link Generation
    * Migrate All Projects to Kicad 7
    * Revert "small test pcb change"
    This reverts commit 8684a29d87f8170850efcf9ba644541f0bce3b16.
    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
    [17-thermistor-7-probe.kicad_sch, 20-thermistor-group-4-probes.kicad_sch, 24-thermistor-group.kicad_sch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]
2023-09-04 Add Mock Inverter (#219)
    * Set up kicad files
    * Fix directories, add initial components for mock inverter
    * Remove old components
    * Add 3 position right angle Micro-Fit 3 symbol to library
    * Add MAX7221 to parts library
    * Add 4 digit 7-segment display symbol to parts library
    * Add ADC to parts library
    * Tweak 4 digit 7-segment display symbol
    * Tweak MAX7221 symbol
    * Add isolated DCDC converter to parts library
    * Add resistors for resistor divider and DCDC converter to schematic
    * Spec DC bus capacitors
    * Add 1A 5V LDO to parts library
    * Add digital isolator for SPI to parts library
    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
    [20-SOIC.STEP, 21-0042B_24_MXM.step, 3AG_fuse_holder.stp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]
2023-09-08 Add IMU Rev 2.1 (#242)
    * Replace 5V and 1V8 LDOs with more common parts
    * Update front and back silkscreens
    [6-WDFN.stp, imu.kicad_pcb, imu.kicad_sch]
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2023-09-24 R2 of MKVI Dashboard Pi Hat (#246)
    after resolving the second-most painful merge conflict of my life, which in typical git fashion, could have actually been fixed with one command, finally merging this.
    * Dashboard Firmware First Draft
    * Updated Dashboard Firmware (post spring break)
    * Added firmware functionality, 10 millisecond delay, interrupts, LED logic, and more
    * Refactored by removing STATES_DICTIONARY and incorporating Amit
    * Snakecased non-constants, fixed callbacks, renamed dashboard to dashboard_message
    * Moved MCP right, AMS to pin 36, RTD to 32, TX0RTs to 15, CS to 18
    * Updated pin numbers from hardware changes
    * Moved CS from to 24, BOTS to 18, ESTOP to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
    [MCP25625.kicad_sch, dashboard.kicad_pcb, dashboard.kicad_sch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]
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2024-02-10 Add MKVI Throttle Firmware (#227)
    * Complete Throttle Firmware First Draft
    * Update CAN Debugging Code
    * Push throttle BUILD file
    * Fix compilation errors
    * Fix CAN init throttle debug error
    * Format bazel BUILD file
    * Update MKVI DBC file to include throttle yml, update throttle BUILD to use MKVI dbc
    * Comment out btldr lines for testing
    * Comment out btldr files for testing
    * Formatting, changed CAN message throttle_state to throttle_status
    * Resolve feedback from draft 1
    * Resolve brake implaus logic error
    * Change throttle pot names to R an L
    * Fix throttle state error
    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
    [throttle.c, throttle_config.h]
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2024-02-10 Refactor HitL software for composability (#237)
    * Continue refactor of hitl code
    * More tests
    * More tests and changes for bringup
    * Add CANController
    * More tests and starting integration tests
    * All HitL chips work
    * Reorganize HitL
    * Refactor python deps
    * Revert testing changes
    * format bazel
    * Update python requirements from btldr
    * Remove old HitL software
    * Deprecate old AIR Control tests
    * Fix issues in CAN controller
    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
    [air.c, utils.py]
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

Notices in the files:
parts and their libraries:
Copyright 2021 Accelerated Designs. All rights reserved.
